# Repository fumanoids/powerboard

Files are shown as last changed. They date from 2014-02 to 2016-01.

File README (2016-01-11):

           README FOR THE POWER BOARD HARD- AND SOFTWARE RELEASE
           =====================================================

          2016-01-11 FUmanoids' Powerboard Hardware Release v2016

          Copyright (c) 2016 FUmanoids / Freie Universität Berlin
                            All rights reserved

        For full license information, please refer to file LICENCE

Links:
       FUmanoids Homepage                           http://www.fumanoids.de
       FUmanoids on Facebook              http://www.facebook.com/fumanoids
       FUmanoids on Twitter                    http://twitter.com/fumanoids

       RoboCup Homepage                              http://www.robocup.org
       RoboCup Humanoid League Homepage          http://www.tzi.de/humanoid

This is part of the code/hardware release of team FUmanoids, version 2016. 

Our goal by releasing the source code and CAD files of components of our robot
is to provide some insight in humanoid soccer robot development, allowing other
teams to learn from our code and possibly our mistakes, but also to hopefully
encourage them to do the same and release their code as well. Though RoboCup is
a competition, it's also about research and finally to achieve our common goal -
to win against FIFA in 2050 ...

 1. PROJECT STRUCTURE
----------------------

The FUmanoids team has developed several software applications as well as our
own robots. The latter was developed internally and equipped with both
commercially available and self-built electronics.

This release addresses only the custom-built power board used in the FUmanoid
robots.

Neither a compiler, an SDK or CAD software is part of this package. In the
section "Getting Started" you find a list of recommended software to modify or
view the CAD files, to compile the software and to put the binaries onto the
processors.

 1.1 Overview of the package
-----------------------------

The project's root directory is "powerboard" (the board's name).

The directories in the root directory are:

 - bin      -- some useful scripts and programs for building the program and
               documentation
 - obj      -- All binary files of the program go here. This directory will
               be created during code compilation.
 - doc      -- The documentation directory. Here you can find some 
               documentation of the board.
 - src      -- The actual source code.
               Note: The essential parts of the software is pretty well
               documented. Please consider this as a documentation 
               directory as well.
 - hardware -- Here you can find the CAD files for the PCB.

 2. THE POWERBOARD PROJECT
------------------------- 

 2.1 Getting Started
-------------------------

 2.1.1 Software

The software is written in C with two extensions in assembler
(system_mutex_lock() and system_mutex_unlock()).

A compiler for the target hardware is not part of this package but can be picked
based on the user's preferences. We recommend using the arm-none-eabi-toolchain
(including gcc, ld and gdb) which can be found here:

                  https://launchpad.net/gcc-arm-embedded/+download

 2.1.2 Hardware

To view the schematics and layout of this project we recommend using "CadSoft
EAGLE" which can be found at: http://www.cadsoftusa.com/

 2.1.3 Manufacturing

The PCB can be manufactured by most commonly known PCB services. A partlist can
be found in the folder where the schematics reside. But please double check the 
partlist since we cannot guarantee its completeness.

We chose every component on the board to be manually solderable. All you need is
a steady hand. And preferably a rework station.

 2.1.4 Other Prerequisites
 
To flash the target an ARM compatible JTAG is needed.

We recommend using an "JLink" from Segger.
There is numerous software available for all major operating systems supporting
the programmer (Linux, Mac, Windows). 

 2.2 Compiling the Software
---------------------------

To compile for debug run: make
To build a release build: RELEASE=1 make

The common IDE used for development in team FUmanoids is Eclipse/CDT which
is available at http://www.eclipse.org. Therefore we have the corresponding
project files added to our repository, to give an easy start. You can build the
code either by using Eclipse or by shell tools. Both ways are easy.
Other IDEs or editors can of course be used.

The build process generates a .elf file which can be flashed on the target.

 2.2.1 Using Eclipse

If you choose to use Eclipse click File->Import and in the opening window
General->"Existing Project into Workspace" and choose the project's root
directory. Then you can compile the debug or release version of the software.

 2.2.2 Using the shell tools

You can simply run

 make

to compile the code.

 2.3 Flashing the target
------------------------

In order to flash the target you need an JTAG. We recommend using the 
Segger/JLink software to communicate with the JTAG and as tool to download 
code onto the target.

If you have JLinkGDBServer installed you can use 

JLinkGDBServer -if swd
make flash 

to flash the target.

 4. REFERENCES
--------------

The framework used in this software was developed as part of the FUmanoid
project and is used in it's sensor board as well (the project can be found
at http://www.fumanoids.de/hardware/erolf). The Berlin United Racing Team
incorporates a microcontroller board similar to the power board which is
operated by the framework as well.

Many aspects of our work is described in the corresponding theses of our
students, which are available online at http://www.fumanoids.de/publications,
though most of them are in German.

 5. CONTACT
-----------

We'd love to receive feedback, please feel free to contact us by email
at info@fumanoids.de. For information about our team and ongoing progress,
follow us on https://www.facebook.com/fumanoids, https://twitter.com/fumanoids
and http://www.fumanoids.de.

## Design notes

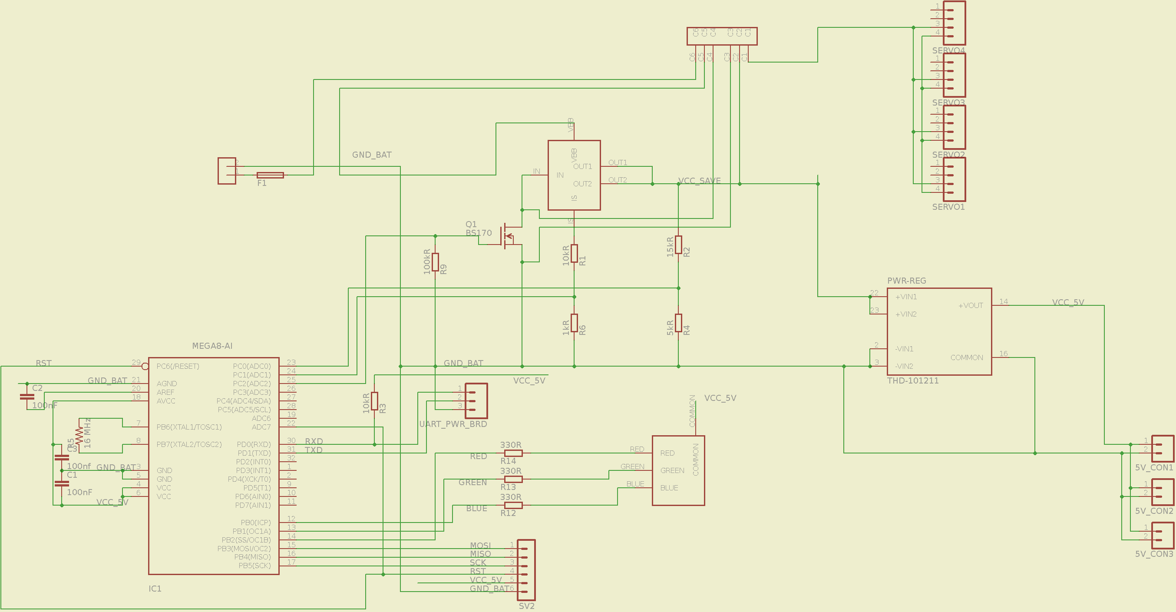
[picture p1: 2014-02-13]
doc/board/schematic.png

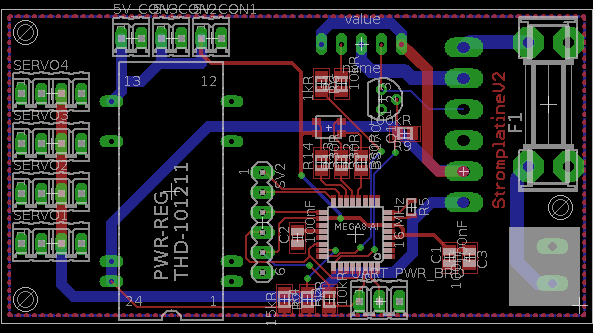
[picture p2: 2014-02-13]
doc/board/borad.png

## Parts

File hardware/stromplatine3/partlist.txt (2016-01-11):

Partlist

Exported from stromplatine3.brd at 10.11.15 11:30

EAGLE Version 6.6.0 Copyright (c) 1988-2014 CadSoft

Assembly variant: 

Part           Value          Package     Library       Position (mm)         Orientation

#### vorrätig:
4x
5V_CON1                       02P         con-amp-quick (68 3)                R90
3x
BUTTONS                       04P         con-amp-quick (25 24)               R270
7x
C6             0.1uF          C0603       resistor      (57 19.1)             R180
1x
F1                            SHK20Q      fuse          (5 15)                R270
1x
J1                            10X05MTA    con-amp       (28 3)                R0
1x
U$3            RGB-LED        4-PLCC      smd-rgbled    (31 26)               R90
5x
R2             1kR            R0603       resistor      (15 15)               MR0
2x
R1             100kR          R0603       resistor      (11 12)               MR90
8x
R6             10kR           R0603       resistor      (39.5 10.5)           MR270
1x
R10            68R            R0603       resistor      (30 21)               R270
1x
R11            82R            R0603       resistor      (32 17)               R270
1x
R12            82R            R0603       resistor      (32 21)               R270
2x
Q1                            SOT23       adafruit      (44 12)               MR90
1x
U$1                           UFQFPN32    stm32f051     (30 12)               R0
1x
U$2                           SOT-23-5    stromplatine  (22 10)               R270
2x
U$4                           TO-252      stromplatine  (15 6)                R180

#### nicht vorrätig:
3x
C2             47uF           C1206       resistor      (56 23.5)             R180
http://www.digikey.com/product-detail/en/CL31A476MQHNNNE/1276-1167-1-ND/3889253

2x
C12            470uF          175TMP-0810 resistor      (64 25)               R180
http://www.digikey.com/product-search/en?vendor=0&keywords=493-3771-1-ND

3x
C11            10uF           C1206       resistor      (49.5 18)             MR90
http://www.digikey.com/product-detail/en/TMK316F106ZL-T/587-1353-1-ND/931130

2x
D_FREILAUF                    DO-214AC    diode         (65 26)               MR90
http://www.digikey.com/product-detail/en/S1G/S1GFSCT-ND/965720

1x
R6             10kR           R0603       resistor      (39.5 10.5)           MR270
http://www.digikey.com/product-detail/en/RC1608F103CS/1276-3485-1-ND/3903588

1x
R5             1.5kR (1%)     R0603       resistor      (51 24)               MR270
http://www.digikey.com/product-detail/en/RC1608F152CS/1276-4660-1-ND/3967632

1x
R31            390R (1%)      R0603       resistor      (49 24)               MR90
http://www.digikey.com/product-detail/en/RC1608F391CS/1276-4610-1-ND/3967582

2x
U$6                           QFN-12-EX   stromplatine  (65 13)               MR0
http://www.digikey.com/product-detail/en/ACS711EEXLT-15AB-T/620-1481-1-ND/3868196

1x
U$11                          TZA11A      stromplatine  (41 22)               R90
http://www.digikey.com/product-detail/en/LMZ12010TZE%2FNOPB/296-40327-1-ND/5178204

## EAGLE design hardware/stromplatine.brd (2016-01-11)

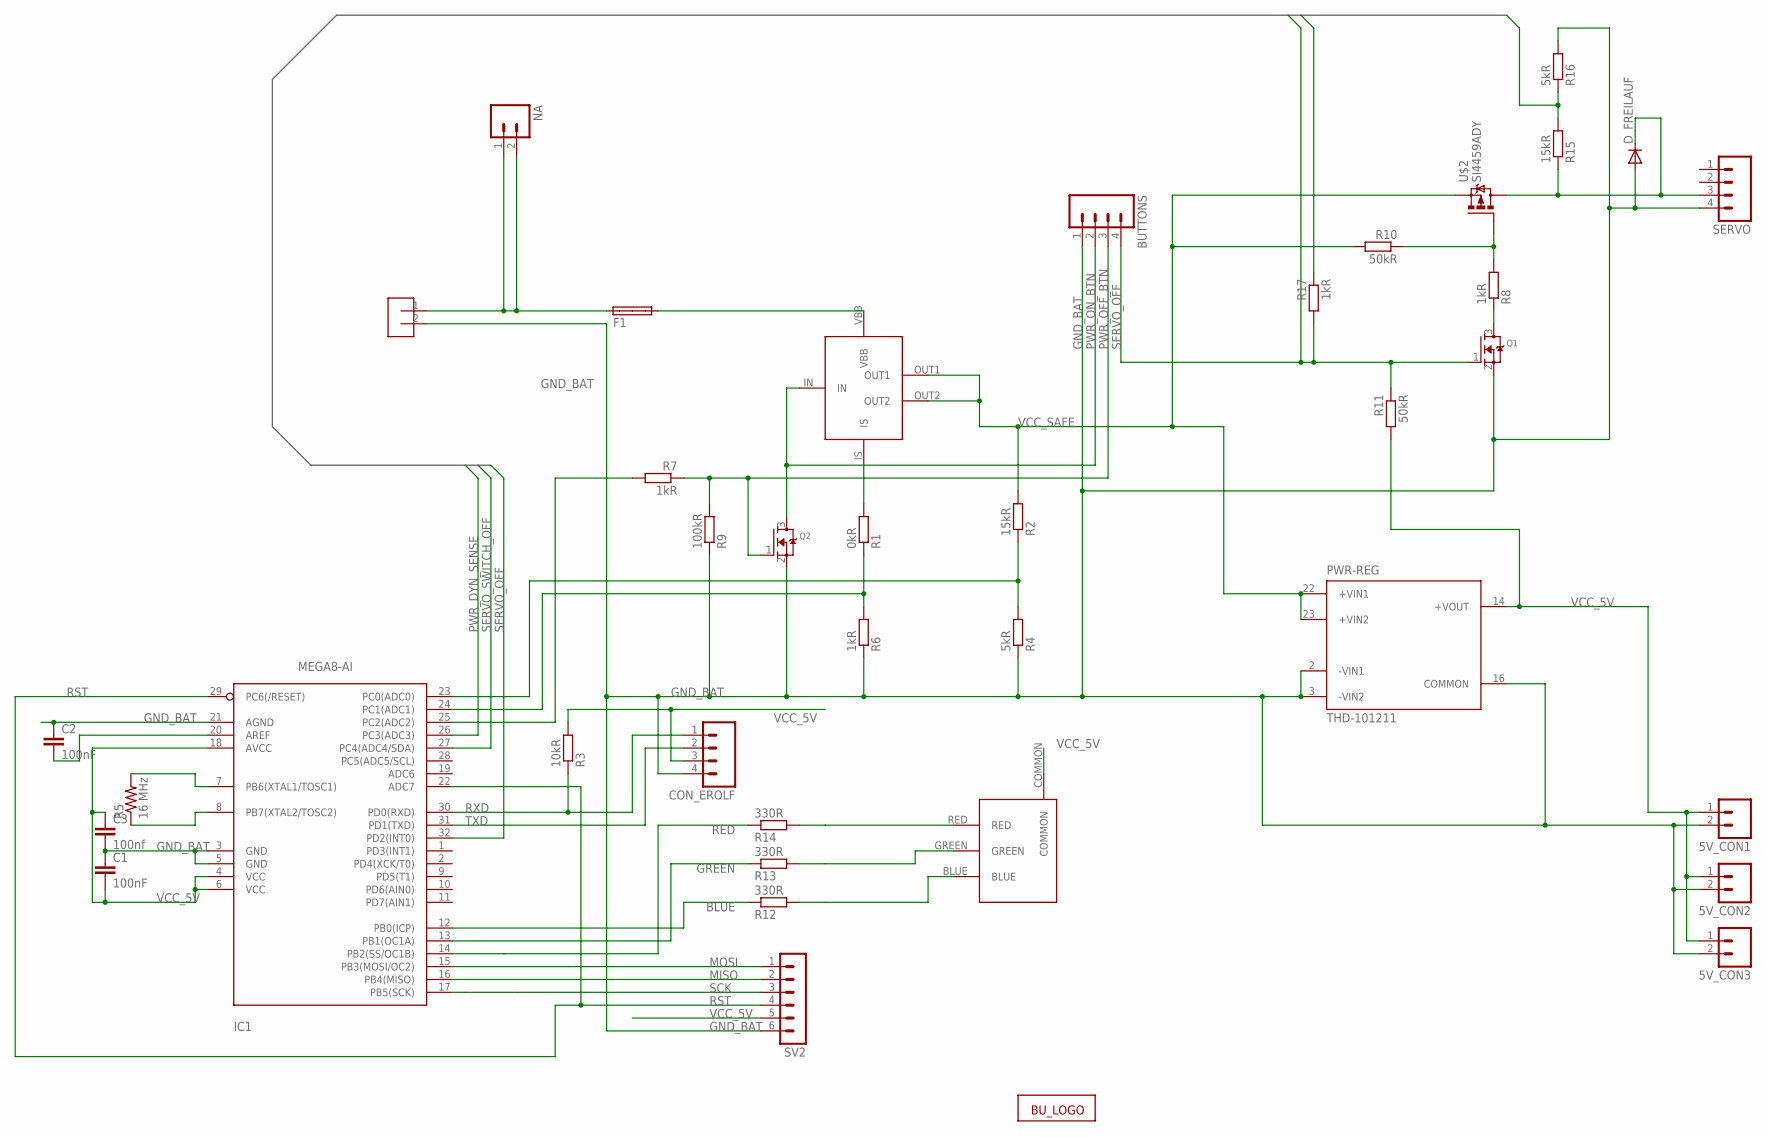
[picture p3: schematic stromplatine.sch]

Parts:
5V_CON1, 5V_CON2, 5V_CON3: M02; 02P
BUTTONS: M04; 04P
C1, C2: 100nF; C0805
C3: 100nf; C0805
CON_BAT: STROMSTECKER
CON_EROLF: M04; 04P
D_FREILAUF: DIODE-DO-214AC; DO-214AC
F1: SHK20Q
IC1: MEGA8-AI; TQFP32-08
NA: M02; 02P
PWR-REG: THD-101211; TEN3XXXX
Q1, Q2: MOSFET-NREFLOW; SOT23
R1: 0kR; M0805
R2, R15: 15kR; M0805
R3: 10kR; M0805
R4, R16: 5kR; M0805
R5: 16 MHz; MINI_MELF-0102W
R6, R7, R8, R17: 1kR; M0805
R9: 100kR; M0805
R10, R11: 50kR; M0805
R12, R13, R14: 330R; M0805
SERVO: M04; 04P
SV2: MA06-1
U$1: BTS555; PG-TO218
U$2: SI4459ADY; SO-8
U$3: RGB-LED; 4-PLCC
U$4: LOGO

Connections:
BLUE: IC1.12 (PB0(ICP)), R12.1
GND_BAT: 5V_CON1.2, 5V_CON2.2, 5V_CON3.2, BUTTONS.1, C1.1, C2.1, C3.2, CON_BAT.2, CON_EROLF.4, D_FREILAUF.A, IC1.3 (GND), IC1.5 (GND), IC1.21 (AGND), PWR-REG.2 (-VIN1), PWR-REG.3 (-VIN2), PWR-REG.16 (COMMON), Q1.2 (S), Q2.2 (S), R4.1, R6.1, R9.1, R16.2, SERVO.4, SV2.6
GREEN: IC1.13 (PB1(OC1A)), R13.1
MISO: IC1.16 (PB4(MISO)), SV2.2
MOSI: IC1.15 (PB3(MOSI/OC2)), SV2.1
unnamed: F1.2A, U$1.VBB
unnamed: CON_BAT.1, F1.1A, NA.1, NA.2
unnamed: IC1.7 (PB6(XTAL1/TOSC1)), R5.2
unnamed: R12.2, U$3.BLUE
unnamed: R13.2, U$3.GREEN
unnamed: IC1.8 (PB7(XTAL2/TOSC2)), R5.1
unnamed: IC1.23 (PC0(ADC0)), R2.1, R4.2
unnamed: D_FREILAUF.C, R15.1, SERVO.3, U$2.P5 (D), U$2.P6 (D), U$2.P7 (D), U$2.P8 (D)
unnamed: C2.2, IC1.20 (AREF)
unnamed: R8.2, R10.1, U$2.P4 (G)
unnamed: IC1.24 (PC1(ADC1)), R1.1, R6.2
unnamed: R1.2, U$1.IS
unnamed: Q1.3 (D), R8.1
unnamed: R14.2, U$3.RED
unnamed: IC1.25 (PC2(ADC2)), R7.2
PWR_DYN_SENSE: IC1.26 (PC3(ADC3)), R15.2, R16.1
PWR_OFF_BTN: BUTTONS.3, Q2.1 (G), R7.1, R9.2
PWR_ON_BTN: BUTTONS.2, Q2.3 (D), U$1.IN
RED: IC1.14 (PB2(SS/OC1B)), R14.1
RST: IC1.22 (ADC7), IC1.29 (PC6(/RESET)), SV2.4
RXD: CON_EROLF.1, IC1.30 (PD0(RXD)), R3.1
SCK: IC1.17 (PB5(SCK)), SV2.3
SERVO_OFF: BUTTONS.4, IC1.32 (PD2(INT0)), Q1.1 (G), R11.1, R17.2
SERVO_SWITCH_OFF: IC1.27 (PC4(ADC4/SDA)), R17.1
TXD: CON_EROLF.2, IC1.31 (PD1(TXD))
VCC_5V: 5V_CON1.1, 5V_CON2.1, 5V_CON3.1, C1.2, C3.1, CON_EROLF.3, IC1.4 (VCC), IC1.6 (VCC), IC1.18 (AVCC), PWR-REG.14 (+VOUT), R3.2, R11.2, SV2.5, U$3.COMMON
VCC_SAFE: PWR-REG.22 (+VIN1), PWR-REG.23 (+VIN2), R2.2, R10.2, U$1.OUT1, U$1.OUT2, U$2.P1 (S), U$2.P2 (S), U$2.P3 (S)

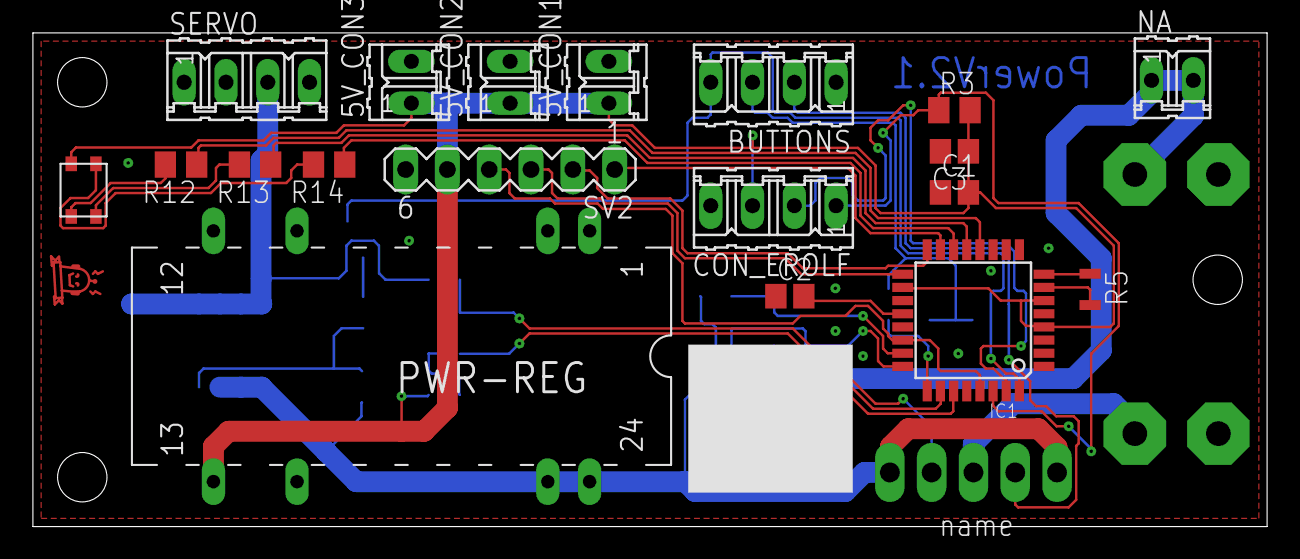
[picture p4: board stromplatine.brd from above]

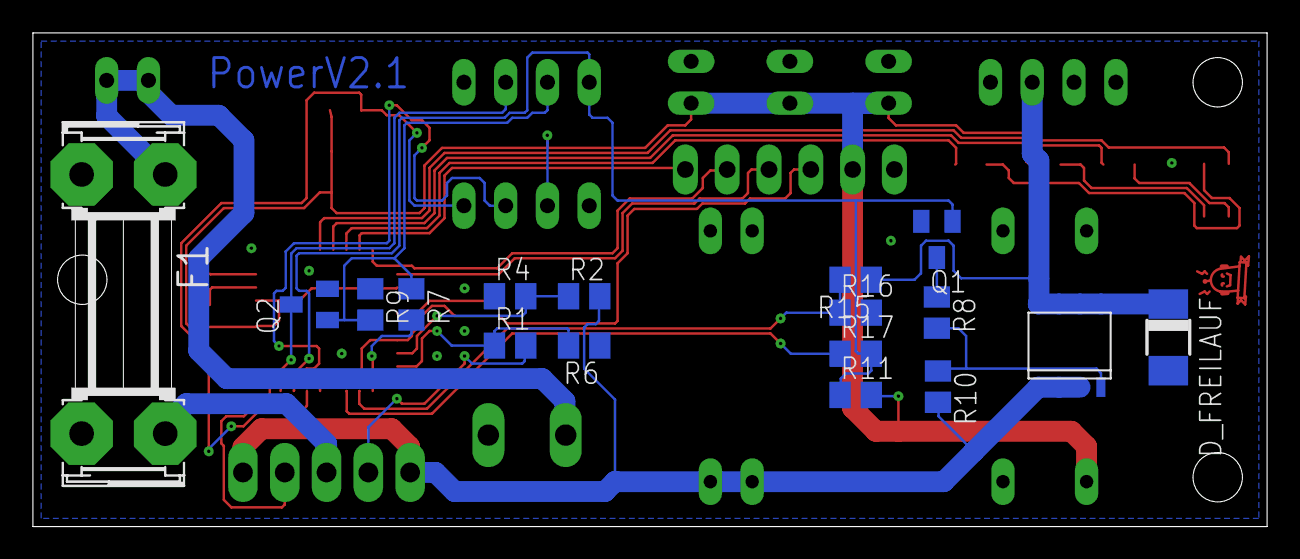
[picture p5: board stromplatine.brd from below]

Board: 2 copper layers, 75.0 x 30.0 mm, 39 parts (17 on the bottom side), 32 nets.

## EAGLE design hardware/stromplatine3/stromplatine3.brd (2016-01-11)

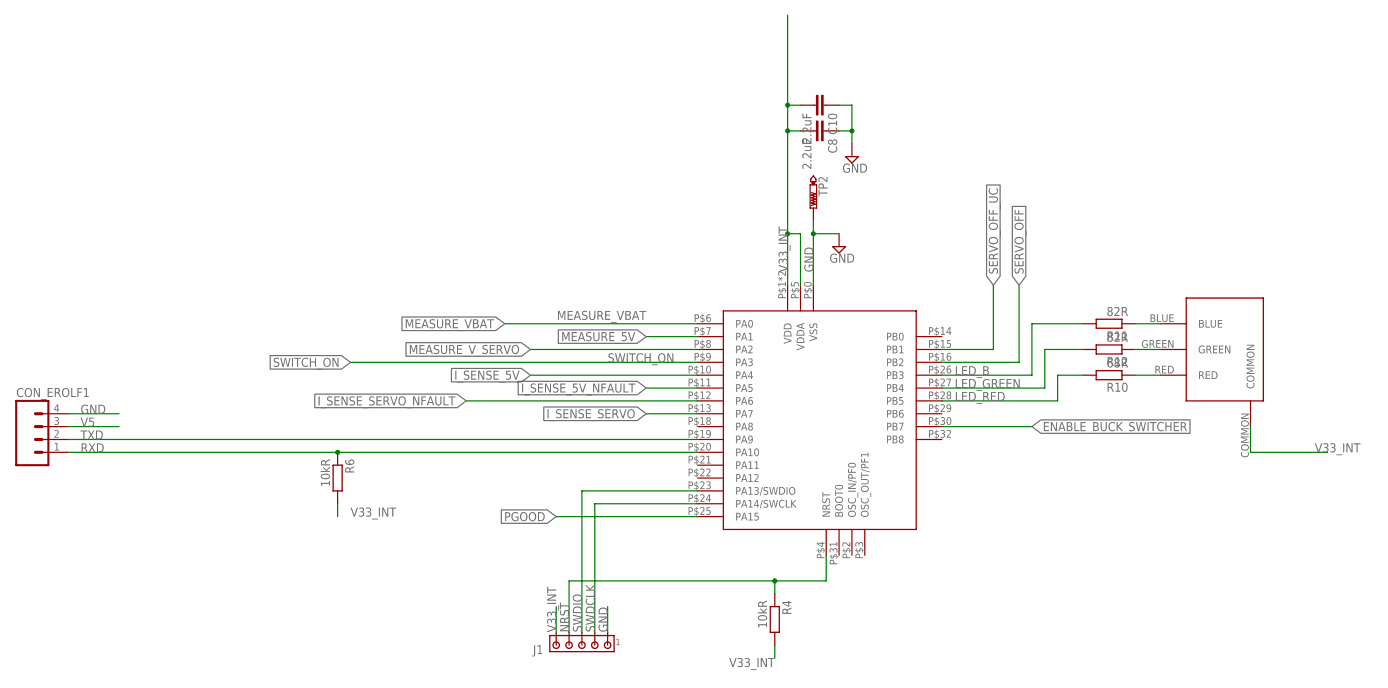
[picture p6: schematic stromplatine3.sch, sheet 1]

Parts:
C8, C10: 2.2uF; C0402
CON_EROLF1: M04; 04P
J1: MTA05-100; 10X05MTA
R4, R6: 10kR; R0603
R10: 68R; R0603
R11, R12: 82R; R0603
TP2: PTR1B1,27; B1,27
U$1: STM32F051K8; UFQFPN32
U$3: RGB-LED; 4-PLCC

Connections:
ENABLE_BUCK_SWITCHER: U$1.P$30 (PB7); also elsewhere on the board
GND: C8.1, C10.1, CON_EROLF1.4, J1.1, TP2.TP, U$1.P$0 (VSS); also elsewhere on the board
I_SENSE_5V: U$1.P$10 (PA4); also elsewhere on the board
I_SENSE_5V_NFAULT: U$1.P$11 (PA5); also elsewhere on the board
I_SENSE_SERVO: U$1.P$13 (PA7); also elsewhere on the board
I_SENSE_SERVO_NFAULT: U$1.P$12 (PA6); also elsewhere on the board
LED_B: R11.2, U$1.P$26 (PB3)
LED_GREEN: R12.2, U$1.P$27 (PB4)
LED_RED: R10.2, U$1.P$28 (PB5)
MEASURE_5V: U$1.P$7 (PA1); also elsewhere on the board
MEASURE_VBAT: U$1.P$6 (PA0); also elsewhere on the board
MEASURE_V_SERVO: U$1.P$8 (PA2); also elsewhere on the board
unnamed: R10.1, U$3.RED
unnamed: R12.1, U$3.GREEN
unnamed: R11.1, U$3.BLUE
NRST: J1.4, R4.1, U$1.P$4 (NRST)
PGOOD: U$1.P$25 (PA15)
RXD: CON_EROLF1.1, R6.1, U$1.P$20 (PA10)
SERVO_OFF: U$1.P$16 (PB2); also elsewhere on the board
SERVO_OFF_UC: U$1.P$15 (PB1)
SWDCLK: J1.2, U$1.P$24 (PA14/SWCLK)
SWDIO: J1.3, U$1.P$23 (PA13/SWDIO)
SWITCH_ON: U$1.P$9 (PA3); also elsewhere on the board
TXD: CON_EROLF1.2, U$1.P$19 (PA9)
V5: CON_EROLF1.3; also elsewhere on the board
V33_INT: C8.2, C10.2, J1.5, R4.2, R6.2, U$1.P$1 (VDD), U$1.P$5 (VDDA), U$1.P$17 (VDD), U$3.COMMON; also elsewhere on the board

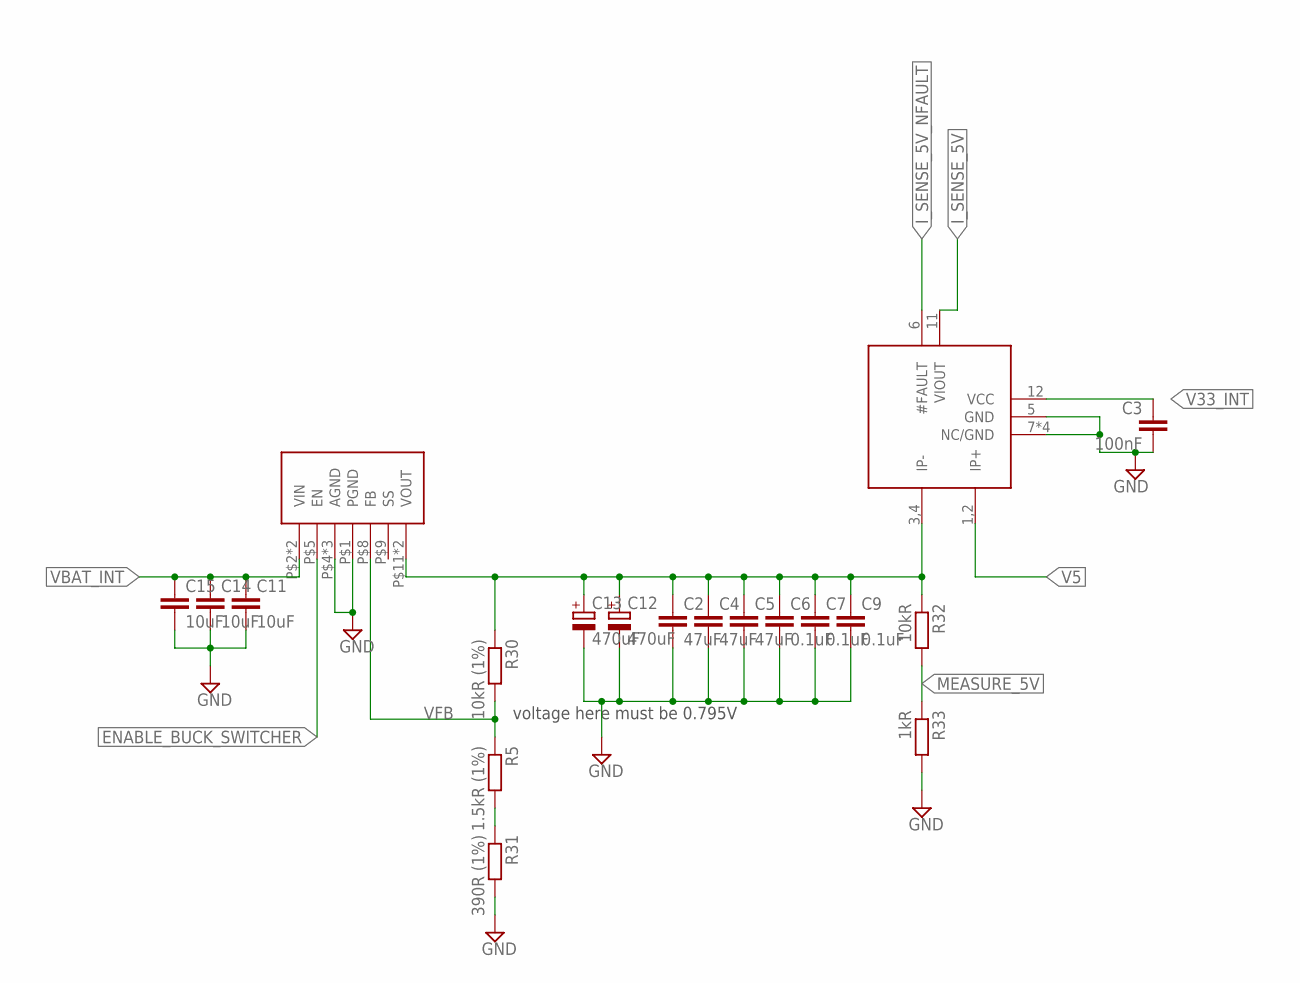
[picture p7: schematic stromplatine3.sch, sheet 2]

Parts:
C2, C4, C5: 47uF; C1206
C3: 100nF; C0402
C6, C7, C9: 0.1uF; C0603
C11, C14, C15: 10uF; C1206; DIGIKEY 587-1353-1-ND
C12, C13: 470uF; 175TMP-0810; DIGIKEY 493-3771-1-ND
R5: 1.5kR (1%); R0603
R30: 10kR (1%); R0603
R31: 390R (1%); R0603
R32: 10kR; R0603
R33: 1kR; R0603
U$10: ACS711; QFN-12-EX
U$11: LMZ12010; TZA11A

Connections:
ENABLE_BUCK_SWITCHER: U$11.P$5 (EN); also elsewhere on the board
GND: C2.2, C3.2, C4.2, C5.2, C6.2, C7.2, C9.2, C11.2, C12.-, C13.-, C14.2, C15.2, R31.2, R33.2, U$10.5 (GND), U$10.7 (NC/GND), U$10.8 (NC/GND), U$10.9 (NC/GND), U$10.10 (NC/GND), U$11.P$1 (PGND), U$11.P$4 (AGND), U$11.P$6 (AGND), U$11.P$7 (AGND); also elsewhere on the board
I_SENSE_5V: U$10.11 (VIOUT); also elsewhere on the board
I_SENSE_5V_NFAULT: U$10.6 (#FAULT); also elsewhere on the board
MEASURE_5V: R32.2, R33.1; also elsewhere on the board
unnamed: R5.2, R31.1
unnamed: C2.1, C4.1, C5.1, C6.1, C7.1, C9.1, C12.+, C13.+, R30.1, R32.1, U$10.3,4 (IP-), U$11.P$11 (VOUT), U$11.P$12 (VOUT)
V5: U$10.1,2 (IP+); also elsewhere on the board
V33_INT: C3.1, U$10.12 (VCC); also elsewhere on the board
VBAT_INT: C11.1, C14.1, C15.1, U$11.P$2 (VIN), U$11.P$3 (VIN); also elsewhere on the board
VFB: R5.1, R30.2, U$11.P$8 (FB)

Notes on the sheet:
voltage here must be 0.795V

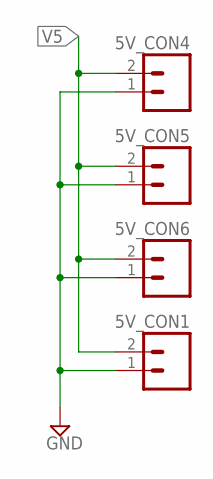
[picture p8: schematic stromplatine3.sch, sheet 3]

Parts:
5V_CON1, 5V_CON4, 5V_CON5, 5V_CON6: M02; 02P

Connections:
GND: 5V_CON1.1, 5V_CON4.1, 5V_CON5.1, 5V_CON6.1; also elsewhere on the board
V5: 5V_CON1.2, 5V_CON4.2, 5V_CON5.2, 5V_CON6.2; also elsewhere on the board

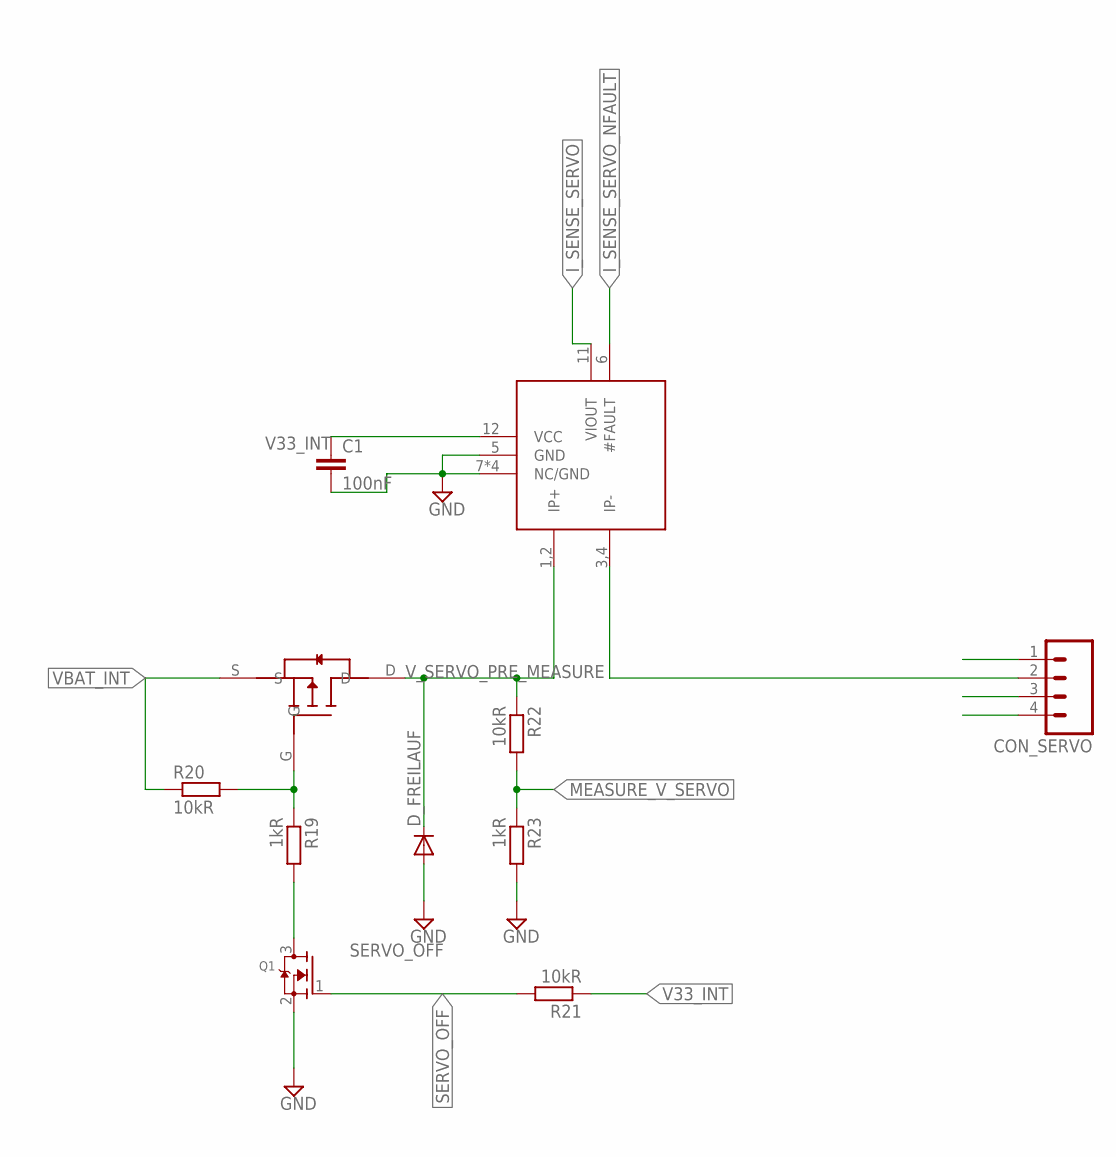
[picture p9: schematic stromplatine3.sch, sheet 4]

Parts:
C1: 100nF; C0402
CON_SERVO: M04; 04P
D_FREILAUF: DIODE-DO-214AC; DO-214AC
Q1: MOSFET-NREFLOW; SOT23
R19, R23: 1kR; R0603
R20, R21, R22: 10kR; R0603
U$6: ACS711; QFN-12-EX
U$7: MOSFET/AOD417; TO-252

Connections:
GND: C1.2, CON_SERVO.1, D_FREILAUF.A, Q1.2 (S), R23.2, U$6.5 (GND), U$6.7 (NC/GND), U$6.8 (NC/GND), U$6.9 (NC/GND), U$6.10 (NC/GND); also elsewhere on the board
I_SENSE_SERVO: U$6.11 (VIOUT); also elsewhere on the board
I_SENSE_SERVO_NFAULT: U$6.6 (#FAULT); also elsewhere on the board
MEASURE_V_SERVO: R22.2, R23.1; also elsewhere on the board
unnamed: Q1.3 (D), R19.2
unnamed: R19.1, R20.2, U$7.G
RS485_SERVO_A: CON_SERVO.3
RS485_SERVO_B: CON_SERVO.4
SERVO_OFF: Q1.1 (G), R21.2; also elsewhere on the board
V33_INT: C1.1, R21.1, U$6.12 (VCC); also elsewhere on the board
VBAT_INT: R20.1, U$7.S; also elsewhere on the board
V_SERVO: CON_SERVO.2, U$6.3,4 (IP-)
V_SERVO_PRE_MEASURE: D_FREILAUF.C, R22.1, U$6.1,2 (IP+), U$7.D

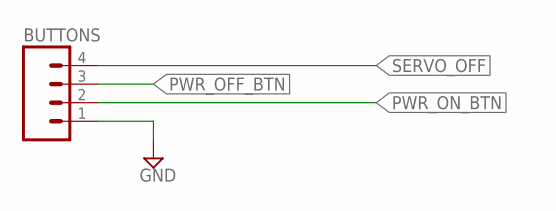
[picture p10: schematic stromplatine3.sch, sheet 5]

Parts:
BUTTONS: M04; 04P

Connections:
GND: BUTTONS.1; also elsewhere on the board
PWR_OFF_BTN: BUTTONS.3; also elsewhere on the board
PWR_ON_BTN: BUTTONS.2; also elsewhere on the board
SERVO_OFF: BUTTONS.4; also elsewhere on the board

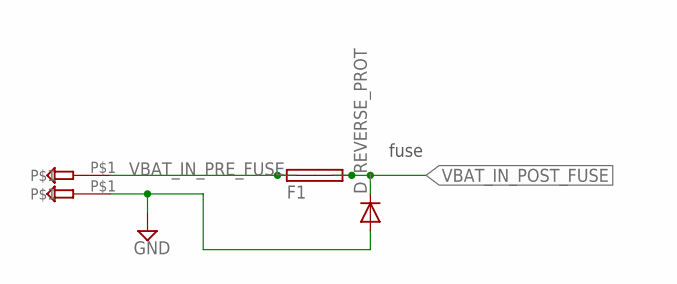
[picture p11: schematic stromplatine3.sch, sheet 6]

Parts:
D_REVERSE_PROT: DIODE-DO-214AC; DO-214AC
F1: SHK20Q
U$8, U$9: TP

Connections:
GND: D_REVERSE_PROT.A, U$9.P$1; also elsewhere on the board
VBAT_IN_POST_FUSE: D_REVERSE_PROT.C, F1.2A, F1.2B; also elsewhere on the board
VBAT_IN_PRE_FUSE: F1.1A, F1.1B, U$8.P$1

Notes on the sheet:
fuse

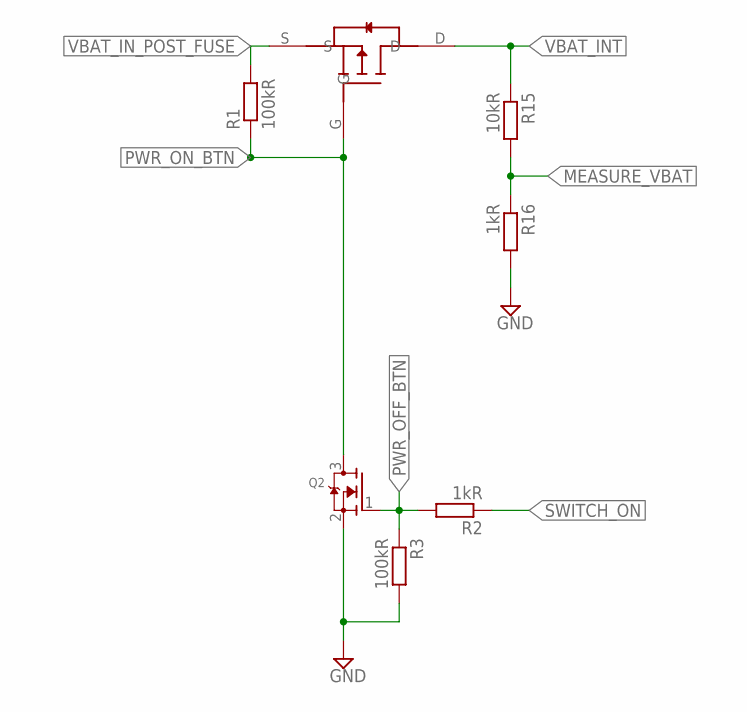
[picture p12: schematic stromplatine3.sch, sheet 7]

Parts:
Q2: MOSFET-NREFLOW; SOT23
R1, R3: 100kR; R0603
R2, R16: 1kR; R0603
R15: 10kR; R0603
U$4: MOSFET/AOD417; TO-252

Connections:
GND: Q2.2 (S), R3.2, R16.2; also elsewhere on the board
MEASURE_VBAT: R15.2, R16.1; also elsewhere on the board
PWR_OFF_BTN: Q2.1 (G), R2.2, R3.1; also elsewhere on the board
PWR_ON_BTN: Q2.3 (D), R1.1, U$4.G; also elsewhere on the board
SWITCH_ON: R2.1; also elsewhere on the board
VBAT_INT: R15.1, U$4.D; also elsewhere on the board
VBAT_IN_POST_FUSE: R1.2, U$4.S; also elsewhere on the board

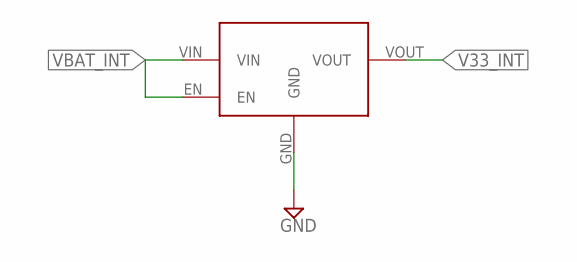
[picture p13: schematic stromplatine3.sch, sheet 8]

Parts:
U$2: LDO/AP2204; SOT-23-5

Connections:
GND: U$2.GND; also elsewhere on the board
V33_INT: U$2.VOUT; also elsewhere on the board
VBAT_INT: U$2.EN, U$2.VIN; also elsewhere on the board

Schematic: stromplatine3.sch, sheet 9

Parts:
U$5: LOGO

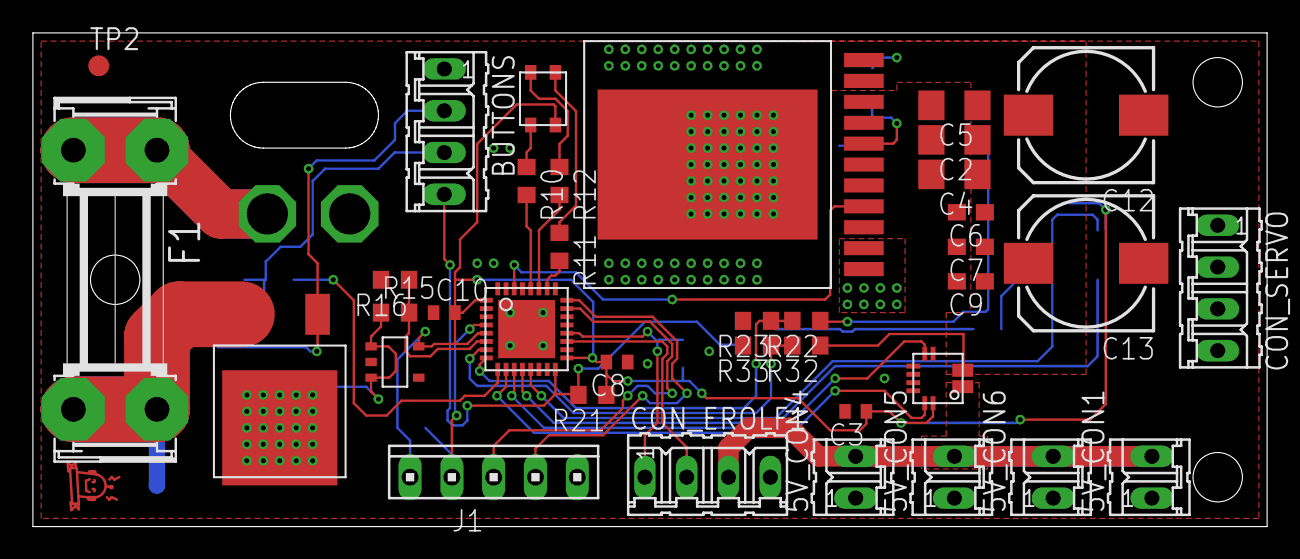
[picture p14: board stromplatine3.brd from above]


Board: 2 copper layers, 75.0 x 30.0 mm, 60 parts (20 on the bottom side), 36 nets.

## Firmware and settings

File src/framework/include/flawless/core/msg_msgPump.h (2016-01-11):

/*
 * msg_msgPump.h
 *
 *  Created on: 26.09.2011
 *      Author: lutz
 */

#ifndef MSG_MSGPUMP_H_
#define MSG_MSGPUMP_H_

#include <flawless/stdtypes.h>
#include <flawless/misc/Assert.h>
#include <flawless/config/msgPump_config.h>


/**
 * define used to declare and statically allocate memory for a message queue including it's needed memory and overhead
 */

typedef uint8_t msgBufPos_t;	  /* the number of a message in the buffer (not the index!) */
typedef uint8_t msgBufRefCount_t; /* the reference count of one message*/
typedef uint16_t msgBufMsgSize_t; /* the size of an actual message in bytes */

typedef uint8_t msgBufBufData_t; /* the type of the elements in the buffer */

typedef uint8_t msgPump_callbackCount_t;
typedef int16_t msgPump_MsgID_t;

/**
 * typedef for a callback function for the message queue
 * the function gets the msgID the data of the current message (a cast is necessary inside the callback function) and the info which was specified during the registration
 */
typedef void (*msgPump_callbackFunction_t)(msgPump_MsgID_t, const void *);


typedef enum en_msgPump_MessageBufferFlag
{
	MsgPump_MsgBufFlagNothing = 0,
	MsgPump_MsgBufFlagPostedNotDispatched = 1 << 0,
	MsgPump_MsgBufFlagInUse = 1 << 1,

	/* this can happen if some software does not use the loc/unlock mechanisms correctly. A buffer element marked with this will not be usable anymore */
	MsgPump_MsgBufFlagBufferNotUsable = 1 << 2
}msgPump_MessageBufferFlag_t;

typedef struct st_msgPumpMsgHeader
{
#ifdef MSG_PUMP_USE_HEADER_MAGIC
	uint32_t headerMagic;
#endif
	msgBufRefCount_t refCnt;
	msgPump_MessageBufferFlag_t flags;
	uint16_t padding;
}msgPumpMsgHeader_t;

typedef enum en_msgPrioirity
{
	MsgPriorityLow,
	MsgPriorityMedium,
	MsgPriorityHigh
}msgPriority_t;

typedef msgPump_callbackFunction_t msgPumpCallBackVector_t[MAX_AMOUNT_OF_MSG_RECERIVER_PER_MESSAGE];

typedef struct st_msgBufDescription
{
	msgBufBufData_t * const data; 						/* the pointer to the memory region where the message data is stored */
	const msgBufMsgSize_t const msgSize;						/* the size of a message in bytes  */
	const msgBufPos_t const	msgAmount;						/* the amount of messages which can be stored in this buffer */
	const msgPump_MsgID_t const id;							/* the id of this message */
	msgPumpCallBackVector_t * const callbackVector;
}msgBufDescription_t;

#define MSG_BUFFER_MSG_OVERHEAD (sizeof(msgPumpMsgHeader_t))

#define MSG_PUMP_DECLARE_MESSAGE_BUFFER_POOL(bufferName, messageType, bufferSize, messageID) \
		/* the actual memory to be used */\
		msgPumpCallBackVector_t bufferName ## _callbackVector;\
		/* the memory of the buffer is aligned like: refCount1, flag, messageBuf1, refCount2, flag, messageBuf2.. etc */\
		msgBufBufData_t  bufferName ## _data_p [bufferSize * (((sizeof(messageType) + 3) & ~(3)) + MSG_BUFFER_MSG_OVERHEAD)]; \
			\
		__attribute__ ((unused))\
		__attribute__ ((section(".msgPumpDescriptions")))\
		const msgBufDescription_t bufferName ## _description = \
												{ \
													bufferName ## _data_p,	\
													((sizeof(messageType) + 3) & ~(3)),	\
													bufferSize,	\
													messageID,	\
													&bufferName ## _callbackVector, \
												};\

/*
 * register on a message. Adds a callback function to a message
 * @param id the ID of the message to register on
 * @param callbackFunction the function to call if the message occurred
 * @param info the argument to be passed to the callback function
 * @return success. There can be a maximum amount of MAX_AMOUNT_OF_MSG_RECERIVER_PER_MESSAGE receivers per message
 */
bool msgPump_registerOnMessage(const msgPump_MsgID_t id, const msgPump_callbackFunction_t callbackFunction);

/*
 * unregister a function from a message
 * @param id the message's ID to unregister from
 * @param callbackFunction the function to unregister
 */
bool msgPump_unregisterFromMessage(const msgPump_MsgID_t id, const msgPump_callbackFunction_t callbackFunction);

/*
 * post a message into the queue. When doing this the reference count is set to the amount of the callback functions listening on this message
 * @param id the message id message belongs to.
 * @param messageToPost a Pointer to a memory region where the message is. This area has to be equal in size to the messageType which was specified when declaring the buffer.
 * @return success. False if the queue is full.
 */
bool msgPump_postMessage(const msgPump_MsgID_t id, void const* messageToPost);

/**
 * Add a reference to this message to prevent this buffer to be overwritten when a new message was posted.
 * The MessagePump decrements the retain count after each callback function returned so use this function if you need access to that data later.
 * @return success. Returns false if the message cannot be locked any more because an overflow would happen.
 */
bool msgPump_lockMessage(void *messageToPost);

/*
 * unlock a message to signal that it's memory space can be used for the data producer.
 * The retain count will be decremented after a callback function returned.
 * This function has to be called if the retain count was incremented via msgPump_lockMesasge().
 * A Message is considered to be free if the amount of unlocks is equal to the amount of locks.
 * @return success. If this operation causes the reference count to be less 0 false.
 */
bool msgPump_unlockMessage(void *messageToPost);

/*
 * if there is a free (not-locked) buffer element in a messageBuffer it can be locked with this function
 * @return success. false if there is no unused buffer element
 */
bool msgPump_getFreeBuffer(const msgPump_MsgID_t id, void **o_destPtr);

/*
 * The infinite loop of the runtime. Inside this function all the messages are pumped to their recipients.
 */
void msgPump_pumpMessage(void);


#endif /* MSG_MSGPUMP_H_ */

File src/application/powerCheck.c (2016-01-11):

/*------------------------includes---------------------------------*/
#include <flawless/stdtypes.h>
#include <flawless/init/systemInitializer.h>
#include <flawless/protocol/genericFlawLessProtocolApplication.h>
#include <flawless/protocol/genericFlawLessProtocol_Data.h>

#include <flawless/core/msg_msgPump.h>
#include <flawless/config/msgIDs.h>

#include <interfaces/battery.h>
#include <interfaces/configuration.h>
#include <interfaces/led.h>

#include <libopencm3/stm32/gpio.h>
#include <libopencm3/stm32/rcc.h>

/*-----------------------------------------------------------------*/


/*--------------------------defines--------------------------------*/
/*bottom range of the battery*/
static const batteryVoltageLevel_t DEFAULT_LOW_THRESHOLD_VAL_V = 970U;

/*this can be considered FULL*/
static const batteryVoltageLevel_t  DEFAULT_HIGH_THRESHOLD_VAL_V = 1200U;

#define PWR_ENABLE_PORT (GPIOA)
#define PWR_ENABLE_PIN (GPIO3)
/*-----------------------------------------------------------------*/


/*--------------------------variables------------------------------*/
CONFIG_VARIABLE(batteryVoltageLevel_t, g_lowThresh, &DEFAULT_LOW_THRESHOLD_VAL_V);
CONFIG_VARIABLE(batteryVoltageLevel_t, g_highThresh, &DEFAULT_HIGH_THRESHOLD_VAL_V);

/*-----------------------------------------------------------------*/

MSG_PUMP_DECLARE_MESSAGE_BUFFER_POOL(relativeBatteryVoltageBuf, batteryVoltageLevel_t, 2, MSG_ID_RELATIVE_BATTERY_VOLTAGE)


void switchAllOff()
{
	gpio_clear(PWR_ENABLE_PORT, PWR_ENABLE_PIN);
	while(1);
}

/*This function should work now with the f0*/
static void onNewPwrMeasurement(msgPump_MsgID_t i_id, const void* buf);
static void onNewPwrMeasurement(msgPump_MsgID_t i_id, const void* buf)
{
	UNUSED(i_id);
	/* if the current measurement is below the lowThresh well cut the power */
	const systemPowerState_t systemPwr = *((const systemPowerState_t*) buf);
	batteryVoltageLevel_t curLevel = systemPwr.batteryVoltcV;
	if (g_lowThresh >= curLevel)
	{
		switchAllOff();
	}

	relativeBatteryLevel_t level;
	if (curLevel < g_lowThresh)
	{
		level = 0x00;
	} else if (curLevel > g_highThresh)
	{
		level = 0xff;
	} else {
		level = ((uint32_t)(255UL * (curLevel - g_lowThresh))) / (g_highThresh - g_lowThresh);
	}

	uint8_t green = level;
	uint8_t red = 0xff - level;

	if (level >= 128)
	{
		green = 0xff;
		red   = 2 * (255 - level);
	} else
	{
		red = 0xff;
		green   = 2 * level;
	}

	setLEDColor(red, green, 0);


	msgPump_postMessage(MSG_ID_RELATIVE_BATTERY_VOLTAGE, &level);
}

void setLowerVoltageEndoint(const void *ipacket, uint16_t i_packetLen, flawLessInterfaceDescriptor_t i_interfaceDescriptor);
GENERIC_PROTOCOL_ENDPOINT(setLowerVoltageEndoint, 103)
void setLowerVoltageEndoint(const void *ipacket, uint16_t i_packetLen, flawLessInterfaceDescriptor_t i_interfaceDescriptor)
{
	UNUSED(i_interfaceDescriptor);
	if (i_packetLen == sizeof(uint16_t))
	{
		g_lowThresh = *((uint16_t*) ipacket);
		config_updateToFlash();
	}
}

void setUpperVoltageEndoint(const void *ipacket, uint16_t i_packetLen, flawLessInterfaceDescriptor_t i_interfaceDescriptor);
GENERIC_PROTOCOL_ENDPOINT(setUpperVoltageEndoint, 102)
void setUpperVoltageEndoint(const void *ipacket, uint16_t i_packetLen, flawLessInterfaceDescriptor_t i_interfaceDescriptor)
{
	UNUSED(i_interfaceDescriptor);
	if (i_packetLen == sizeof(uint16_t))
	{
		g_highThresh = *((uint16_t*) ipacket);
		config_updateToFlash();
	}
}

void getLimitsEndoint(const void *ipacket, uint16_t i_packetLen, flawLessInterfaceDescriptor_t i_interfaceDescriptor);
GENERIC_PROTOCOL_ENDPOINT(getLimitsEndoint, 101)
void getLimitsEndoint(const void *ipacket, uint16_t i_packetLen, flawLessInterfaceDescriptor_t i_interfaceDescriptor)
{
	UNUSED(i_packetLen);
	UNUSED(ipacket);
	uint16_t reply[2];
	reply[0] = g_lowThresh;
	reply[1] = g_highThresh;
	genericProtocol_sendMessage(i_interfaceDescriptor, 100, sizeof(reply), &reply);
}

/*This seems to be the software power off function*/
/*This function should work now with the f0*/
void masterOff(const void *ipacket, uint16_t i_packetLen, flawLessInterfaceDescriptor_t i_interfaceDescriptor);
GENERIC_PROTOCOL_ENDPOINT(masterOff, 100)
void masterOff(const void *ipacket, uint16_t i_packetLen, flawLessInterfaceDescriptor_t i_interfaceDescriptor)
{
	UNUSED(i_interfaceDescriptor);
	if (i_packetLen > 0U)
	{
		const uint8_t val = *((const uint8_t*)ipacket);
		if (0 != val)
		{
			switchAllOff();
		}
	}
}

/*This seems like a second init function*/
static void pwrCheck_init1(void);
MODULE_INIT_FUNCTION(pwrCheck1, 5, pwrCheck_init1)
static void pwrCheck_init1(void)
{
	RCC_AHBENR |= RCC_AHBENR_GPIOAEN;
	msgPump_registerOnMessage(MSG_ID_SYSTEM_POWER_STATE, &onNewPwrMeasurement);

	// turn on
	gpio_mode_setup(PWR_ENABLE_PORT, GPIO_MODE_OUTPUT, GPIO_PUPD_NONE, PWR_ENABLE_PIN);
	gpio_set_output_options(PWR_ENABLE_PORT, GPIO_OTYPE_PP, GPIO_OSPEED_25MHZ, PWR_ENABLE_PIN);
	gpio_set(PWR_ENABLE_PORT, PWR_ENABLE_PIN);
}


/*-----------------------------------------------------------------*/

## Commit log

2014-02-13 code release 2014
    [powerboard.brd, powerboard.sch]
2016-01-11 Yeyyy the new version of the power board... woooohoooo
    [configuration.h, powerboard.brd, powerboard.sch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]
